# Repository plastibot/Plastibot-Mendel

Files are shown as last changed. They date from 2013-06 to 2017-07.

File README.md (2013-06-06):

Plastibot-Mendel
================

PLASTIC PARTS:

Plastic parts are released under the same license as the original author.

Refer to www.plastibot.com/credits for credits/attributions as well as license for each part.

Print the following quantities of the plastic parts. The Gcode files were sliced using settings tailored
to the Plastibot Mendel Printer. If you have a different printer you will have to slice your own files.
Use 0.25mm layer tickness and 25% infill. The Y-LM8UU holder and the X-Carriage-LM8UU-Holder requires to
add a lip of 2mm to ensure the part won't come loose half print.

1x  X-End Motor
1x  X-End Idler
1x  X-Carriage-Platform
1x  X-Carriage-Bracket
2x  X-Carriage-LM8UU-Holder
1x  Herringbone Big Gear
1x  Herringbone Small Gear
1x  Extruder (Body, idler, spacer, axle)
4x  Y-LM8UU Holder
2x  Y-Belt Clamp sets (channel, clamp and socket)
2x  endstop holder
2x  Fan Holder
2x  Spool Bushing

LASER CUT PARTS:

The Laser cut Frame is released under Creative Commons - Non Commercial Use License.

Laser cut out of 3/16" thick birch plywood. The bed plate needs to be laser cut out of 
MDF 3/8" thick.

ASSEMBLY INSTRUCTIONS

Assembly instructions can be found at:

    www.plastibot.com/assembly-instructions

Remaining parts (vitamins) to build the printer can be purchased at:

    www.plastibot.com/store

For support please contact us at support@plastibot.com

Have fun !!!

The Plastibot Team.

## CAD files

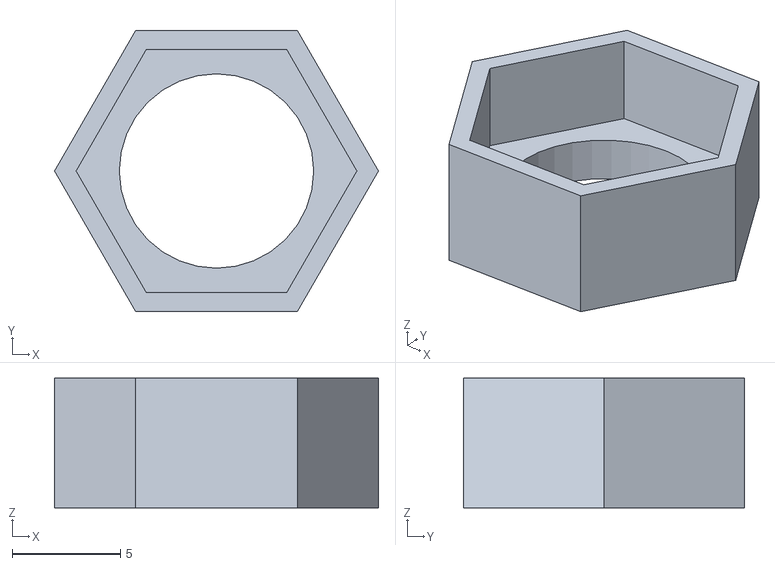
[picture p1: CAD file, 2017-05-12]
Plastic Parts/Backlash spring cup/Spring Cup Rev1.stl
15.0 x 13.0 x 6.00

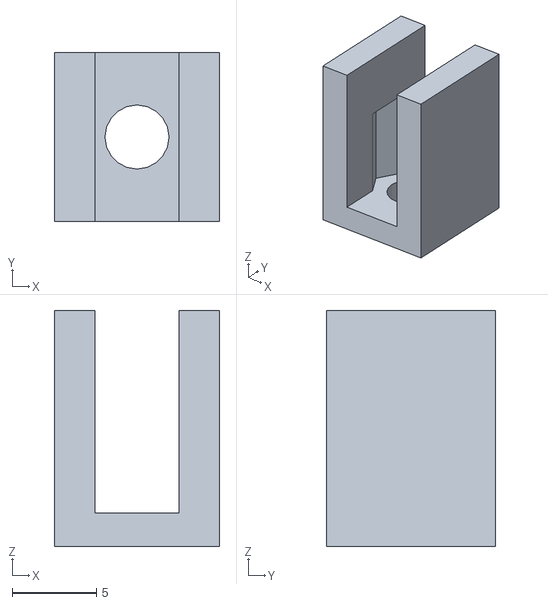
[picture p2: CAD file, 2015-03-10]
Plastic Parts/Card Bracket/Card Bracket 10.stl
9.80 x 10.0 x 14.0

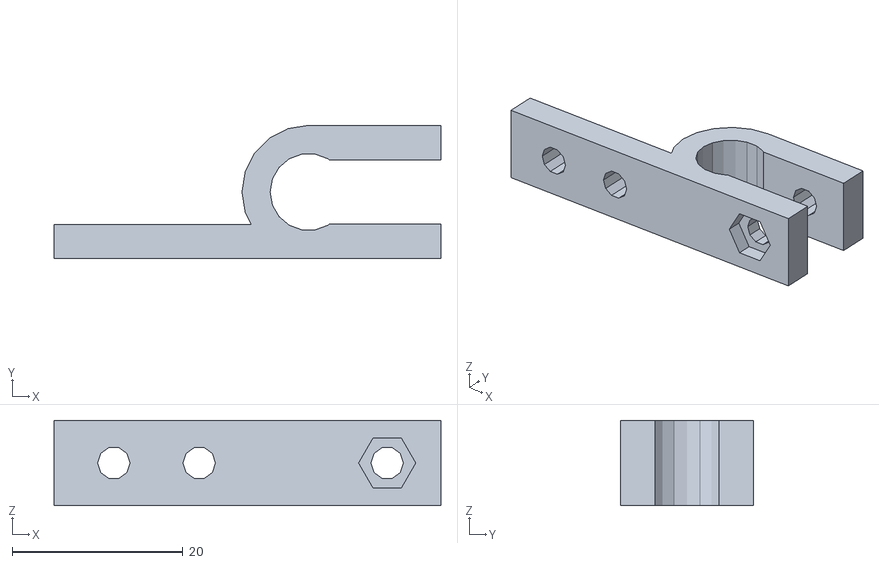
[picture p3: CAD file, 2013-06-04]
Plastic Parts/Endstop Holder/endstop_holder.stl
45.3 x 15.6 x 10.0

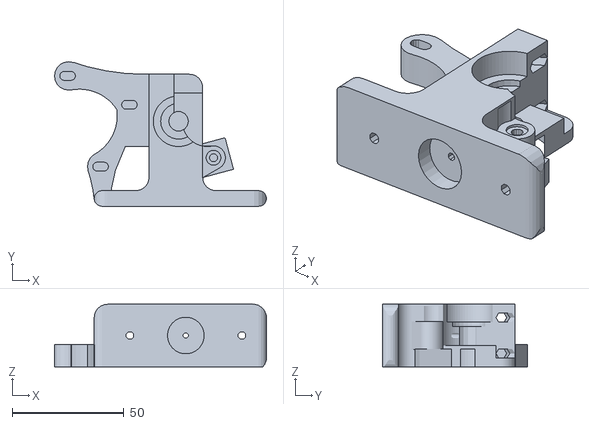
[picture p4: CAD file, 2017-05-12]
Plastic Parts/Extruder 1_75mm Primary/Extruder-primary_body-1_75-fixed.stl
94.7 x 64.6 x 28.0

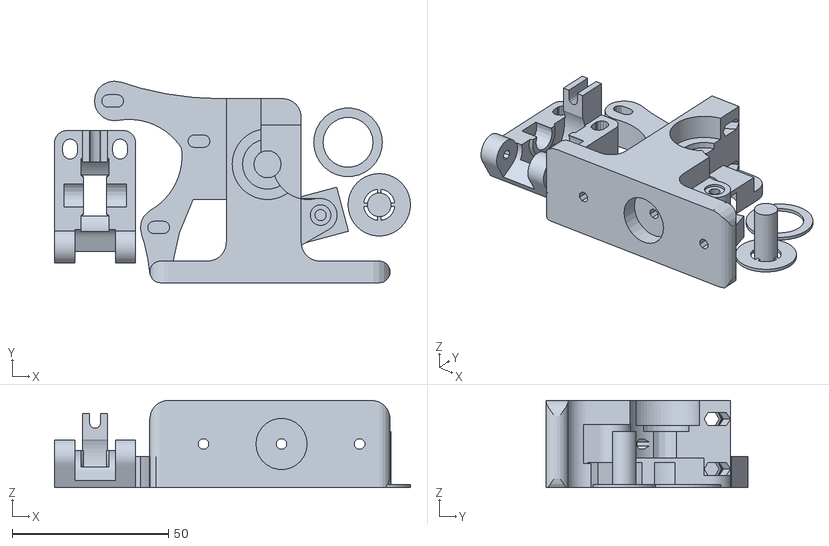
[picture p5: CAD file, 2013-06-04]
Plastic Parts/Extruder 3mm Primary/Extruder-all-parts.stl
114.0 x 64.6 x 28.0

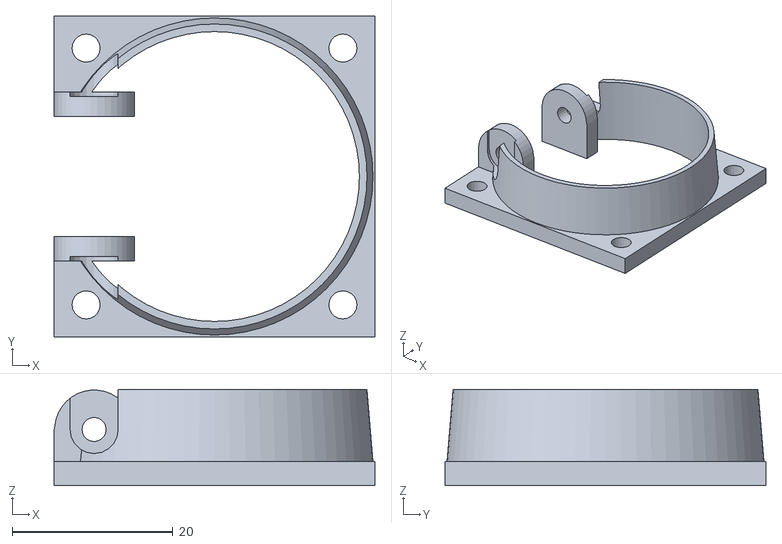
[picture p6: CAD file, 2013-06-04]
Plastic Parts/Fan holder/fanholder.stl
40.0 x 40.0 x 12.0

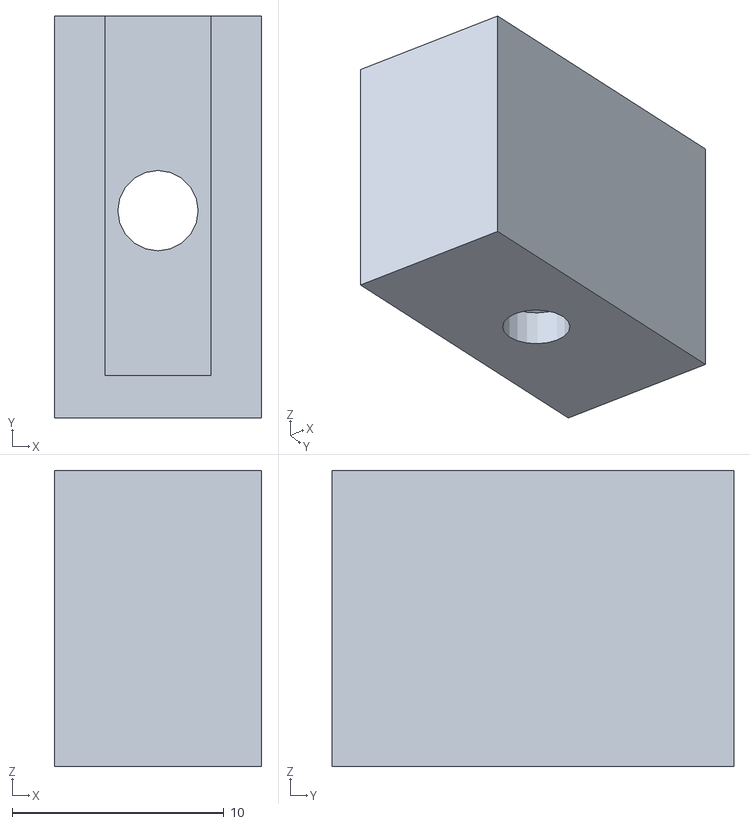
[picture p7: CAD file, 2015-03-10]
Plastic Parts/Frog Bracket/Frog Bracket Rev2.stl
9.80 x 19.0 x 14.0

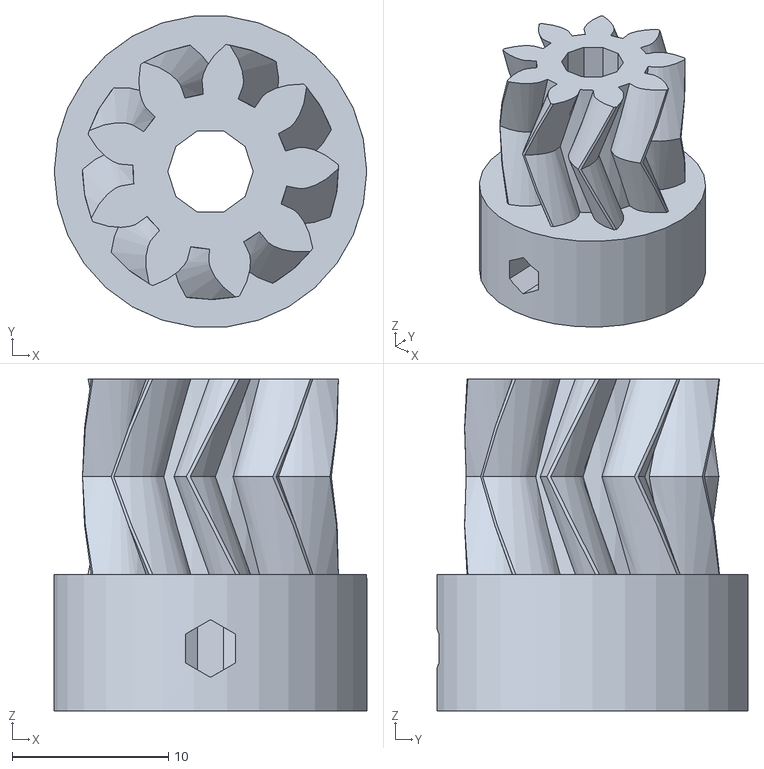
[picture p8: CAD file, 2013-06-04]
Plastic Parts/Herringbone Gears/smallgear.stl
20.0 x 19.9 x 21.2

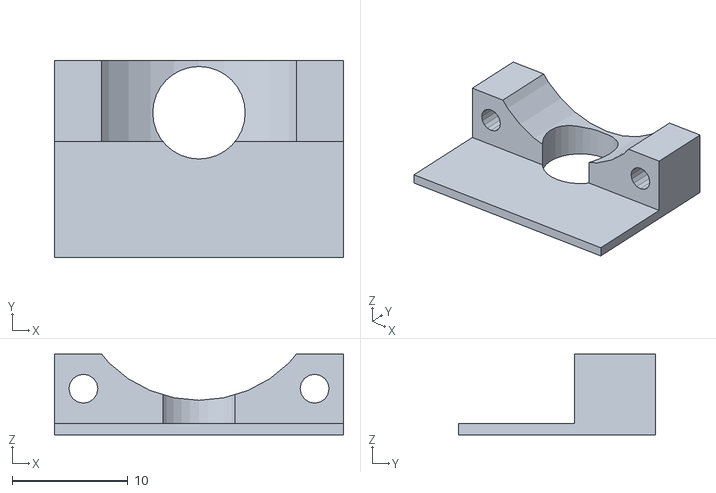
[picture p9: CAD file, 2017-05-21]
Plastic Parts/Hexagon fan/hotend_fan_rev1.stl
25.0 x 17.0 x 7.00

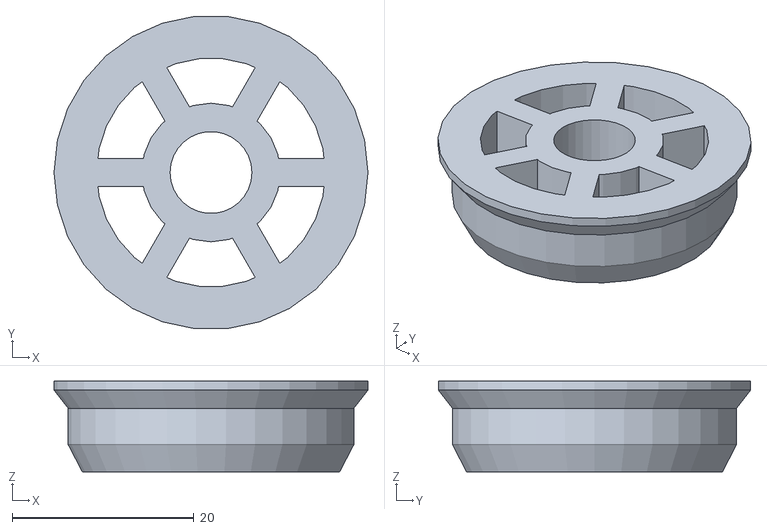
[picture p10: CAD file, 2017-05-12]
Plastic Parts/Spool Bushing/bushing-1Kg-32mm.stl
34.5 x 34.3 x 10.0

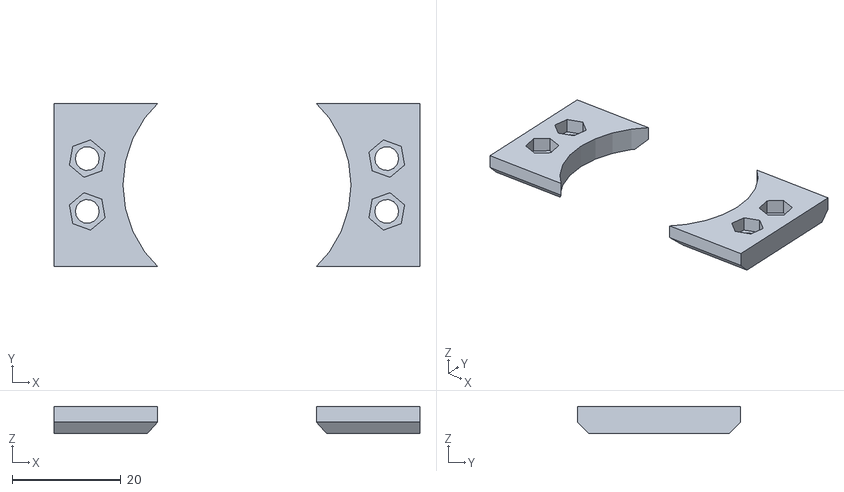
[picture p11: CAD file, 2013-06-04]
Plastic Parts/X carriage/Bracket.stl
67.4 x 30.0 x 5.00

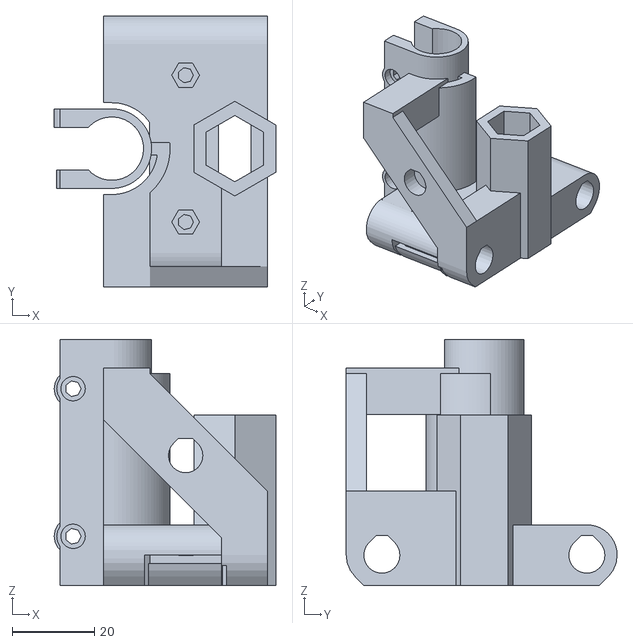
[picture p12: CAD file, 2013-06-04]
Plastic Parts/X supports/x-end-idler.stl
54.1 x 66.0 x 60.0

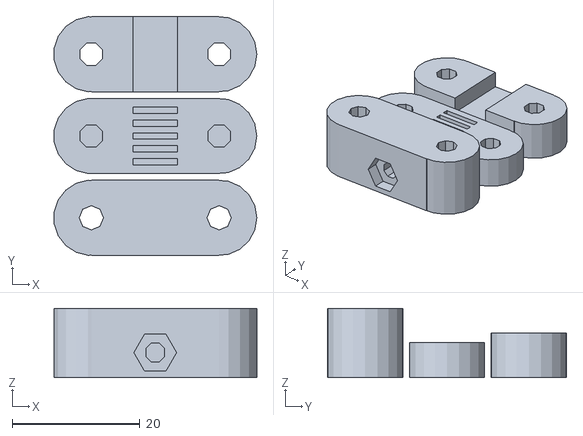
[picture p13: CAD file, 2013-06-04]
Plastic Parts/Y belt clamp/y-belt-clamp.stl
31.7 x 37.4 x 10.8

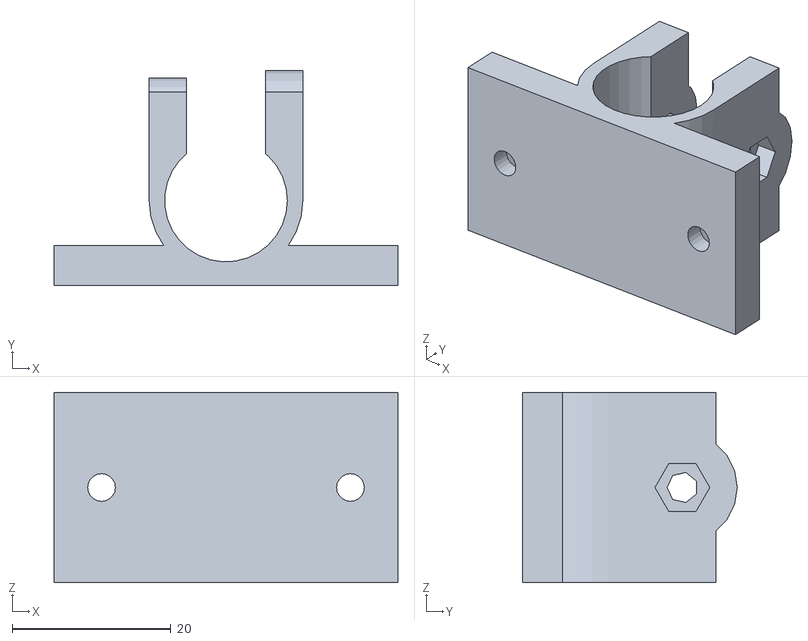
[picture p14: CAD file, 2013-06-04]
Plastic Parts/Y Carriage/y-lm8uu-holder-slim-vertical.stl
43.4 x 27.1 x 24.0

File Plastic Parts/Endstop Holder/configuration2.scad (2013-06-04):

// PRUSA Mendel  
// Configuration file
// GNU GPL v2
// Josef Průša
// josefprusa@me.com
// prusadjs.cz
// http://www.reprap.org/wiki/Prusa_Mendel
// http://github.com/prusajr/PrusaMendel

// PLEASE SELECT ONE OF THE CONFIGURATIONS BELOW
// BY UN-COMMENTING IT

variant=0; //0 for metric
//variant=1; //1 for SAE
if(variant==0){
echo("variant: metric");
}else if(variant==1){
echo("variant: sae");
} else{
echo("WARNING: INVALID CONFIGURATION");
}


vars=[
//[m8_dia, m8_nut, m4_dia, m4_nut, m3_dia, m3_nut, bush_dia, mot_shaft, bush_rod, bush_outerdia, bush_length]
[9,16,4.5,9.3,3.8,6.7,11,5.3,8,16,11],//metric M8 was 15.8
[9,15.4,4.5,9.3,4.5,9.3,11.5,5.3,7.9375,16,11]//SAE
];

//BUSHING TYPE Can generate three versions
// 1 - regular old ones
// 2 - helical ones
// 3 - holders for brass or any other bought bushings
bushing_type = 2;

//Round corner diameter
round_corner_diameter = 8;

//Thin wall size
layer_height = 0.4;
perimeter_width_over_thicknes = 1.6;
infill_widht_over_thickness = 1.55;
thin_wall = 2*(perimeter_width_over_thicknes*layer_height+infill_widht_over_thickness*layer_height);
if(thin_wall<2){
	echo("Check thin wall size, its below 2mm!");
}
echo(thin_wall);

//DO NOT TOUCH THIS SECTION!
m8_diameter = vars[variant][0];
m8_nut_diameter = vars[variant][1];
m4_diameter = vars[variant][2];
m4_nut_diameter = vars[variant][3];
m3_diameter = vars[variant][4];
m3_nut_diameter = vars[variant][5];
bushing_diameter = vars[variant][6];
motor_shaft=vars[variant][7];
bushing_rodsize = vars[variant][8];
bushing_outerDiameter = vars[variant][9];
bushing_lenght = vars[variant][10];


// MINI-HUXLEY VERSION (TODO, just place holder)
// include <configuration-huxley.scad>

// MEGA VERSION (TODO, just place holder)
// include <configuration-mega.scad>


// Some basic functions, probably should be somewhere else
module roundcorner(diameter){
	difference(){
		cube(size = [diameter,diameter,99], center = false);
		translate(v = [diameter, diameter, 0]) cylinder(h = 100, r=diameter, center=true);
	}
}

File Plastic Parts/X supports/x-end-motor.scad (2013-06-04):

// PLASTIBOT MENDEL
// X-end-motor.
// Added room for 32T pulley. Added screw for Z endstop fine adjustment.
// Plastibot <support@plastibot.com>
// Derived from: 

// Improved X ends for Prusa with clamped rods
// by Jonas Kuehling
// http://www.thingiverse.com/thing:18384



use <jonaskuehling-default.scad>
include <lm8uu-holder-slim_double-vertical.scad>



$fa =0.01;
$fs = 1;

// PARAMETERS
rod_dia = 8.4; // was 8
rod_dist = 50;		// center to center
zrod_leadscrew_dist = 30;
clearance = 0.2;		// default clearance
wall = 3;			// default wall thickness
wall_thin = 3;
xend_body_length = 40;

m3_screw_dia = 3; //was 3
m3_screw_head_dia = 6;
m3_screw_head_height = 3;
m3_nut_wrench_size = 5.5; //was 5.5
m3_nut_height = 2.4;

m8_screw_dia = 8; //was 8
m8_washer_dia = 16;
m8_washer_height = 1.5;

idler_dia = 22;		// when using pure 608 bearing without belt guide: 22mm - was 25

belt_rod_dist = 7.5;		// in y direction
belt_elevation = 6.5;		// in z direction, space between rod top and belt bottom;
						// = distance between upper side of rods and upper platform of x-carriage (with belt clamps)
belt_height = 2.6;		// belt thickness..

xmotor_y_offset = 45;
idler_y_offset = rod_dist/2+rod_dia/2+belt_rod_dist - 2*m8_washer_height;

// belt range = rod_dist/2+rod_dia/2+belt_rod_dist - nema17 shaft socket = 36.5 - 43 = 6.5mm

leadscrew_dia = 7; // was 8
leadscrew_nut_wrench_size = 13.4+0.2;		// plus some extra clearance - was 13
leadscrew_nut_height = 6.8;
anti_backlash_spring_space = 25;

nema17_width = 43;
nema17_hole_dist = 31;
nema17_center_dia = 25;

layer_height = 0.25; // was 0.25

xend_body_x_offset = 3;
motor_mount_x_offset = -2;


// CALCULATIONS
xend_body_height = rod_dia+2*clearance+2*wall;
xend_body_width = rod_dist+rod_dia+2*wall;
leadscrew_nuttrap_height = 2*leadscrew_nut_height+wall+anti_backlash_spring_space;
bearing_support_height = leadscrew_nuttrap_height;
idler_elevation = xend_body_height/2+rod_dia/2+belt_elevation+belt_height+idler_dia/2;


// RENDER
// "idler=false" for motor-x-end, "idler=true" for idler-x-end

assembly(idler=false);


difference() {
	union() {
		assembly(idler=false);
		//translate([-17.5, 45, 31.75]) rotate([90, 0, 0]) difference() {
			//cylinder(r=27, h=10);
			//cylinder(r=16, h=50, center=true);
			//rotate([0, 0, 6]) translate([-17, 0, -50]) cube([100, 100, 100]);
			//rotate([0, 0, -30]) translate([-9, -50, -50]) cube([100, 100, 100]);
		//}
		translate([-38,18,0]) difference() {
			cube([10,15,10]);
			translate([5,5,0])
				polyhole(m3_screw_dia+2*clearance,xend_body_height+10);
			translate([5,5,0])
				nut_trap(m3_nut_wrench_size,m3_nut_height+1.6);
		}
		translate([-38,17,m3_nut_height-0.4])
			cube([10,15,0.4]);	
	}
	translate([-17.5, 50, 31.75]) rotate([90, 0, 0]) {
		cylinder(r=15, h=20);
		translate([0, -13, 0]) cube([100, 26, 20]);
		


	}
}




// -------------------------------------------------

module rod_mount(){
	difference(){
		// block for rods
		translate([0,(rod_dist/2+rod_dia/2+wall)/2,0])
			cube([xend_body_length,rod_dist/2+xend_body_height/2,xend_body_height],center=true);
	
		// round corners horizontal
		translate([xend_body_length/2,rod_dist/2+xend_body_height/2,xend_body_height/2])
			rotate([180,90,0])
				roundcorner(xend_body_height/2,xend_body_length);
		translate([xend_body_length/2,rod_dist/2+xend_body_height/2,-xend_body_height/2])
			rotate([0,0,180]) 
				roundcorner_tear(xend_body_height/2,xend_body_length);
	
		// rod hole
		translate([0,rod_dist/2,0]) teardropcentering(rod_dia/2+clearance,xend_body_length+2);
	
		// rod clamp
		translate([0,body_width/2+1,0])
		difference(){
			translate([0,(rod_dist/2+rod_dia/2+wall+1)/2,-(rod_dia/2+wall+1)/2])
				cube([xend_body_length-20,rod_dist/2+rod_dia/2+wall+1,rod_dia/2+wall+1],center=true);
			translate([0,(rod_dist/2+rod_dia/2+wall+1)/2,-(rod_dia/2+wall+1)/2-2])
				cube([xend_body_length-20-2,rod_dist/2+rod_dia/2+wall+1+2,rod_dia/2+wall+1],center=true);
		}
		translate([0,rod_dist/2,-0.1]) teardropcentering_half(rod_dia/2+clearance+1,xend_body_length-20-2-4,bottom=1);
		

		// clamp screw + nut trap + screw-head-trap
		translate([0,rod_dist/2-rod_dia/2-m3_screw_dia/2-2*clearance-1,0])
			polyhole(m3_screw_dia+2*clearance,xend_body_height+2);
		translate([0,rod_dist/2-rod_dia/2-m3_screw_dia/2-2*clearance-1,xend_body_height/2-m3_nut_height/2+0.5])
			nut_trap(m3_nut_wrench_size,m3_nut_height+1);
	}

	// screw hole print support
	translate([0,rod_dist/2-rod_dia/2-m3_screw_dia/2-2*clearance-1,layer_height/2+(xend_body_height/2-layer_height*round((xend_body_height/2)/layer_height))])
		polyhole(m3_screw_dia+2*clearance,layer_height);
}



module bearing_holder(){
	// linear bearing holder
	translate([-zrod_leadscrew_dist/2,0,0])
		rotate([0,0,90])
			lm8uu_holder_slim_double_vertical();
}

module bearing_holder_spacer(){
	render()
	translate([-body_width/2-zrod_leadscrew_dist/2,0,body_length/2])
		cube([body_width,body_width+3,body_length+2], center = true);
	difference(){
		translate([-zrod_leadscrew_dist/2,0,-1])
			cylinder(r=body_width/2+1.5, h=body_length+2);
		translate([body_width/2-zrod_leadscrew_dist/2+body_width/2-0.5,0,body_length/2])
			cube([body_width,body_width+3,body_length+2], center = true);
	}
}



module leadscrew_nuttrap(){
	translate([zrod_leadscrew_dist/2,0,0])
		rotate([0,0,30]){
			translate([0,0,leadscrew_nuttrap_height/2])
				difference(){
					nut_trap(leadscrew_nut_wrench_size+2*wall,leadscrew_nuttrap_height);
					nut_trap(leadscrew_nut_wrench_size,leadscrew_nuttrap_height+2);
				}
			translate([0,0,wall/2+leadscrew_nut_height])
				difference(){
					nut_trap(leadscrew_nut_wrench_size+2*wall,wall);
					rotate([0,0,-30]) cube([leadscrew_dia+1,leadscrew_nut_wrench_size*2,wall+2],center=true);
				}
		}
}

module leadscrew_nuttrap_spacer(){
	translate([zrod_leadscrew_dist/2,0,leadscrew_nuttrap_height/2])
	rotate([0,0,30])
		nut_trap(leadscrew_nut_wrench_size+2*wall,leadscrew_nuttrap_height+2);
}



nema17_hole1 = [nema17_hole_dist/2,nema17_hole_dist/2];
nema17_hole2 = [nema17_hole_dist/2,-nema17_hole_dist/2];
nema17_hole3 = [-nema17_hole_dist/2,nema17_hole_dist/2];
nema17_hole4 = [-nema17_hole_dist/2,-nema17_hole_dist/2];

module motor_mount(){
	difference(){
		union(){
			translate([-nema17_hole_dist/2+motor_mount_x_offset,xmotor_y_offset,
						nema17_hole_dist/2+xend_body_height+m3_screw_dia/2+clearance])
				difference(){
					union(){
						rotate([90,0,0])
							linear_extrude(height=10){
								barbell(nema17_hole3,nema17_hole4,
										(nema17_width-nema17_hole_dist)/2,(nema17_width-nema17_hole_dist)/2,
										20,60);
								barbell(nema17_hole4,nema17_hole2,
										(nema17_width-nema17_hole_dist)/2,(nema17_width-nema17_hole_dist)/2,
										20,60);
							}
		
						// nema17 mount bottom support
						translate([0,-10-(xmotor_y_offset-10-rod_dist/2)/2,
									-xend_body_height/2-nema17_hole_dist/2-m3_screw_dia/2-clearance])
							cube([nema17_width,xmotor_y_offset-10-rod_dist/2,xend_body_height],center=true);
						translate([0,-5,-(xend_body_height+m3_screw_dia/2+clearance)/2-nema17_hole_dist/2])
							difference(){
								cube([nema17_width,10,(xend_body_height+m3_screw_dia/2+clearance)],center=true);

								// round corner bottom x direction
								translate([nema17_width/2,5,-(xend_body_height+m3_screw_dia/2+clearance)/2])
									rotate([0,0,180]) 
										roundcorner_tear(xend_body_height/2,nema17_width);
							}
					}
		
					// nema17 screw holes
					for(k=[1,-1]) for(l=[1,-1])
						translate([k*nema17_hole_dist/2,-5,l*nema17_hole_dist/2])
							rotate([0,0,90]) teardrop(m3_screw_dia/2+clearance,12);
		
					// xend body cut off 1
					translate([0,-(xmotor_y_offset-rod_dist/2)-0.1,-(xend_body_height/2+m3_screw_dia/2+clearance)-nema17_hole_dist/2])
						rotate([180,0,0])
							teardropcentering(xend_body_height/2,nema17_width+2);

					// round corner bottom y direction
					translate([-nema17_width/2,5,-nema17_hole_dist/2-m3_screw_dia/2-clearance-xend_body_height])
						rotate([0,0,-90]) 
							roundcorner_tear(xend_body_height/2,nema17_width);
				}
		
			// nema17 mount top support
			translate([0,0,nema17_hole_dist+(m3_screw_head_dia+2*clearance)/2+xend_body_height+m3_screw_dia/2+clearance])
				linear_extrude(height=5)
					polygon(points=[[-xend_body_length/2+xend_body_x_offset,body_width/2+1.5],[-xend_body_length/2+xend_body_x_offset+10,body_width/2+1.5],
										[-nema17_hole_dist+motor_mount_x_offset+5,xmotor_y_offset],
										[-nema17_hole_dist+motor_mount_x_offset-5,xmotor_y_offset]]);

			translate([-nema17_hole_dist+motor_mount_x_offset,-5+xmotor_y_offset,nema17_hole_dist+xend_body_height+m3_screw_dia/2+clearance+(5+m3_screw_head_dia/2+clearance)/2])
				cube([10,10,5+m3_screw_head_dia/2+clearance],center=true);
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

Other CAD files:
Lasercut Parts/Plastibot Mendel Rev2.6.dwg
Plastic Parts/Backlash spring cup/Spring Cup.stl
Plastic Parts/Card Bracket/Card Bracket 15.stl
Plastic Parts/Extruder 1_75mm Primary/Extruder-idler-primary-1_75.stl
Plastic Parts/Herringbone Gears/parametric_involute_gear_v5.0.scad
Plastic Parts/Backlash spring cup/Spring Cup Rev1.scad
Plastic Parts/Backlash spring cup/Spring Cup.scad
Plastic Parts/Bed-Corners/Bed-Corner-std-nut-3_5mm.scad
Plastic Parts/Bed-Corners/Bed-Corner-std-nut-3_5mm.stl
Plastic Parts/Card Bracket/Card Bracket.scad
Plastic Parts/Endstop Holder/endstop-holder.scad
Plastic Parts/Extruder 1_75mm Primary/Extruder-all-parts-1_75.scad
Plastic Parts/Extruder 3mm Primary/Extruder-all-parts.scad
Plastic Parts/Extruder 3mm Primary/configuration.scad
Plastic Parts/Extruder 3mm Primary/functions.scad
Plastic Parts/Extruder 3mm Primary/gregs-wadebits.scad
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

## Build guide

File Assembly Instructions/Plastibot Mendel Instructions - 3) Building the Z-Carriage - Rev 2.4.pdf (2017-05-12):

# Mendel 3D Printer Assembly

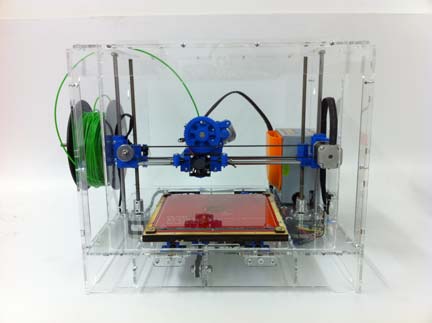
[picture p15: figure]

# Section 3

# Z-Carriage Assembly

## Step 1: Adding the backlash mechanism

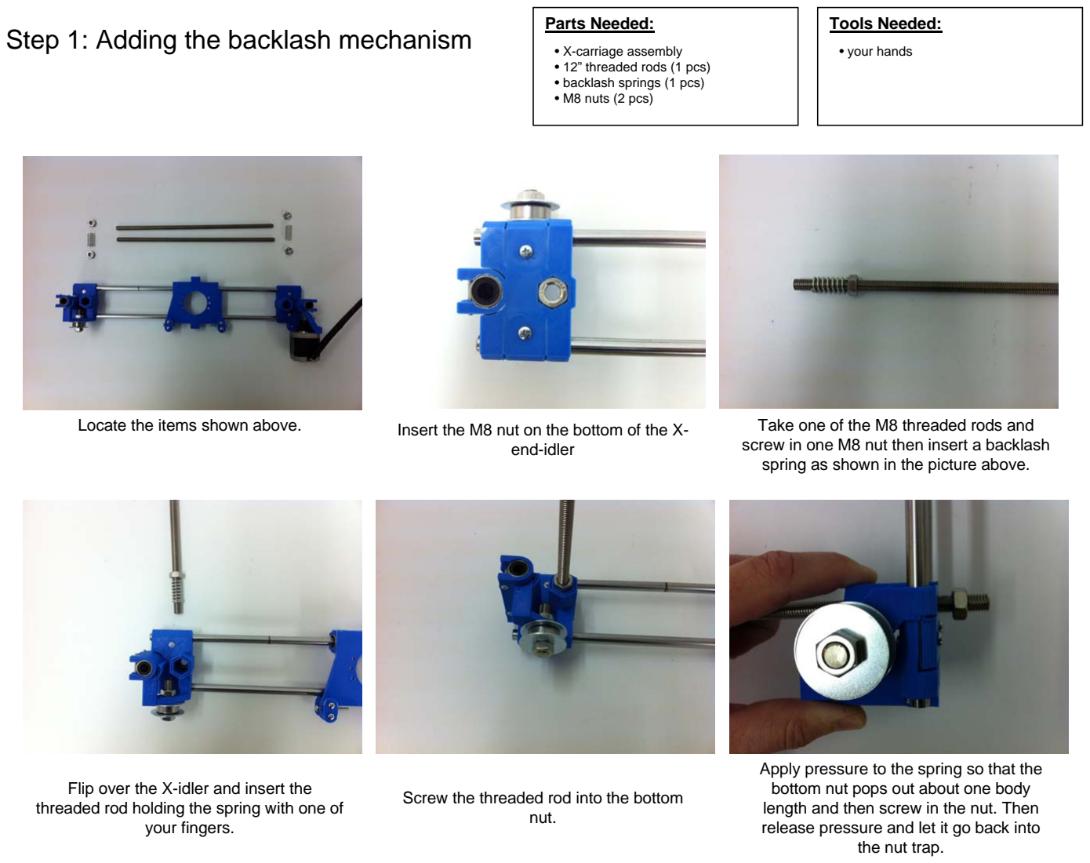
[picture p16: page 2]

Parts Needed:

- X-carriage assembly
- 12” threaded rods (1 pcs)
- backlash springs (1 pcs)
- M8 nuts (2 pcs)

Tools Needed:

- your hands
Locate the items shown above. | Take one of the M8 threaded rods and screw in one M8 nut then insert a backlash spring as shown in the picture above.

Flip over the X-idler and insert the threaded rod holding the spring with one of your fingers.

Apply pressure to the spring so that the bottom nut pops out about one body length and then screw in the nut. Then release pressure and let it go back into the nut trap.

Insert the M8 nut on the bottom of the X-end-idler

Screw the threaded rod into the bottom nut.

## Step 2: Adding the backlash mechanism

(Cont).

Parts Needed:

- X-carriage assembly
- 12” threaded rods (1 pcs)
- backlash springs (1 pcs)
- M8 nuts (2 pcs)

Tools Needed:

- Your hands

Repeat the same steps done on previous page this time for X-end-Motor. Take the second threaded rod, screw-in a nut and insert the backlash spring.

Screw in the bottom nut.

Apply pressure to the spring so that the bottom nut pops out about one body length and then screw in the nut.

This is how it should look now.

Insert the threaded rod with the nut and backlash spring from the top of the X-end-motor assembly

Then release pressure and let it go back into the nut trap.

## Step 3: Adding couplings

Parts Needed:

- X-carriage assembly
- Couplings ( 2 pcs)

Tools Needed:

- Allen Key #2 (Metric)
Locate the parts shown above. | Use the #2 Allen key to unscrew the setscrew until it doesn’t show anymore..

This I show the hole should look after unscrewing the setscrew. Make sure you do this on both holes of each coupling.

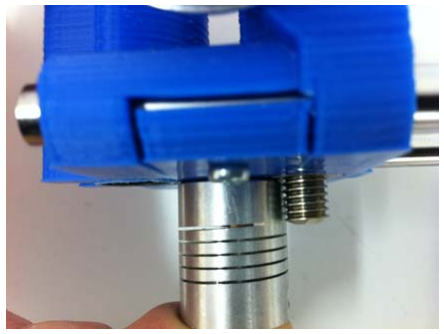
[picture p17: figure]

Face the coupling against the bottom surface right next to the threaded rod and screw in or out the threaded rod so that the end of the threaded rod is where the spiral on the coupling starts.

Make sure the setscrews on the couplings are not obstructing the hole. In this case you can see the setscrew protruding.

Find the hole on the coupling with the bigger diameter

## Step 4: Adding couplings (cont.)

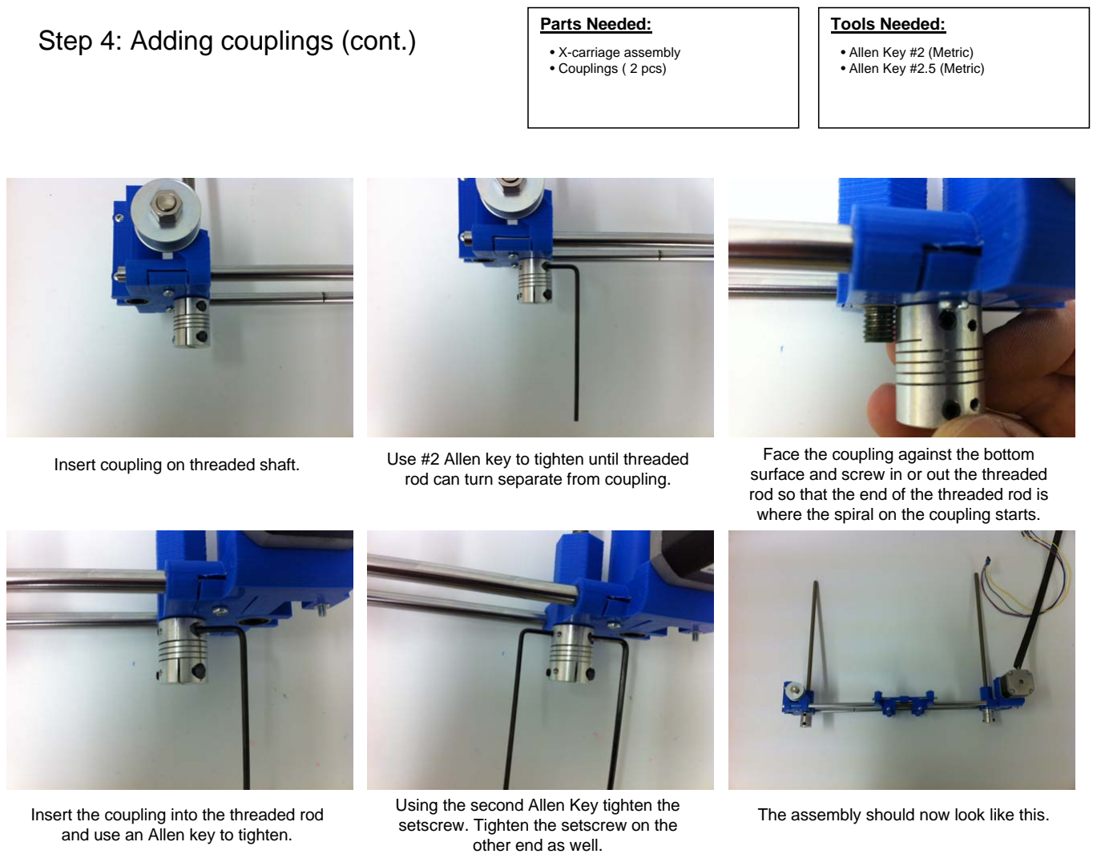
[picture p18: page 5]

Parts Needed:

- X-carriage assembly
- Couplings ( 2 pcs)

Tools Needed:

- Allen Key #2 (Metric)
- Allen Key #2.5 (Metric)
Insert coupling on threaded shaft. | Face the coupling against the bottom surface and screw in or out the threaded
| rod so that the end of the threaded rod is where the spiral on the coupling starts.

Insert the coupling into the threaded rod and use an Allen key to tighten.

The assembly should now look like this.

Use #2 Allen key to tighten until threaded rod can turn separate from coupling.

Using the second Allen Key tighten the setscrew. Tighten the setscrew on the other end as well.

Step 5: Adding Left side Z Smooth rod Parts Needed: • X-carriage assembly • Frame Assembly • Z smooth rods (2 pcs)

Tools Needed:

- Your hands

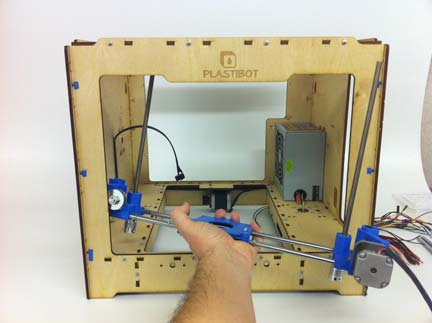
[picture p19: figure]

Take the assembly previously finished and carefully insert it into the frame using the Front window (window with the plastibot logo)

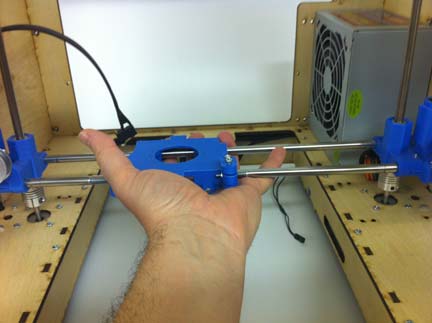
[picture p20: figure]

Align the couplings to the Z-motor shafts and let them sit on top of the shafts

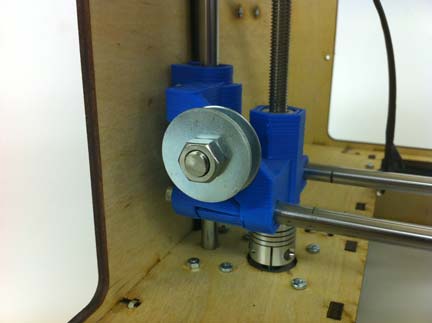
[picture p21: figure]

Align the smooth rod with the bottom hole and push the smooth rod all the way into the bottom panel.

Continue to push down the smooth rod from the top until the rod is flush (or a couple mm) on the top panel

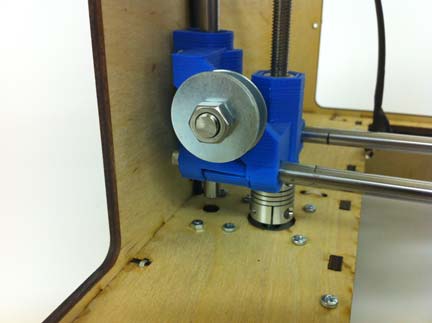
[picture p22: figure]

Align the left side linear bearings with the smooth rod. Keep them as parallel as possible and insert the rod thru the linear bearings.

Insert the Left side Z smooth rod into the hole on the Top Assembly and Lower it to just before the X-end-idle Linear bearings.

NOTE: If the smooth rods are not completely parallel when inserted into the linear bearings, some of the balls on the linear bearing will pop out. That is normal as long as you only get a couple or so out.

Step 6: Adding right side Z Smooth rod Parts Needed: • X-carriage assembly • Frame Assembly • Z smooth rods (2 pcs) • Zip Ties (2 pcs)

Tools Needed:

- Your hands

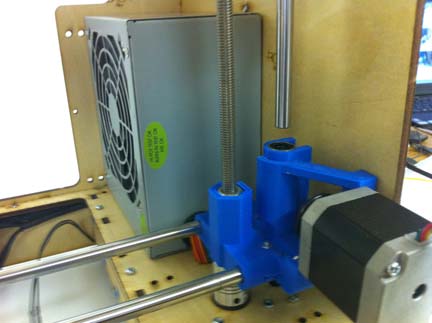
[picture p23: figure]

Insert the Right side Z smooth rod into the hole on the Top Assembly and Lower it to just before the X-end-motor Linear bearings

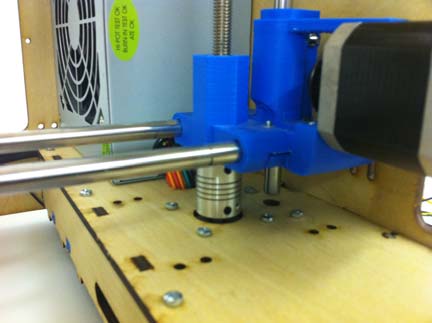
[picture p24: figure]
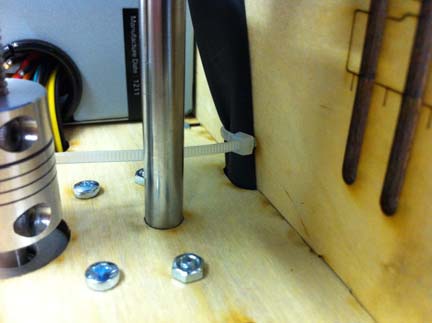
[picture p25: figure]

Use a zip tie to secure the wire harness in place to the left panel at the bottom section.

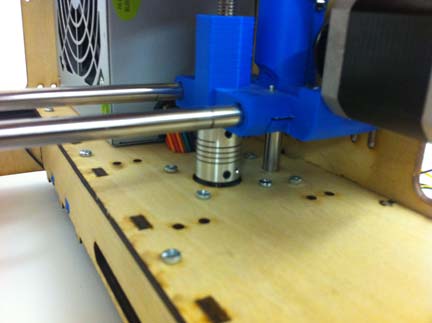
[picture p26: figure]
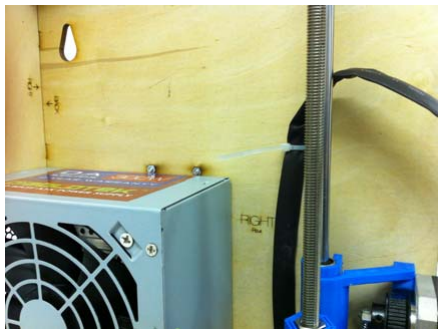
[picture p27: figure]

Use a second zip tie to secure to the left panel at the middle section.

Continue to push down the smooth rod from the top until the rod is flush (or a couple mm) on the top panel.

Align the smooth rod with the bottom hole and push the smooth rod all the way into the bottom panel.

NOTE: If the smooth rods are not completely parallel when inserted into the linear bearings, some of the balls on the linear bearing will pop out. That is normal as long as you only get a couple or so out.

Align the Right side linear bearings with the smooth rod. Keep them as parallel as possible and insert the rod thru the linear bearings.

## Step 7: Tightening couplings to motor shaft

Parts Needed:

- Frame assembly
- laser cut caps (2 pcs)

Tools Needed:

- Allen Key #2 (Metric)
- Allen Key #2.5 (Metric)

Use #2.5 Allen key to tighten the coupler to the motor shaft. If there isn’t enough room to turn the Allen key, then turn the 2 threaded rods to raise the Z axis

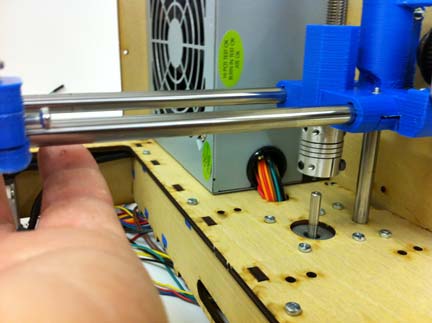
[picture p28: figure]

Align the couplings on both ends to the motor shafts and insert if they arent inserted already.

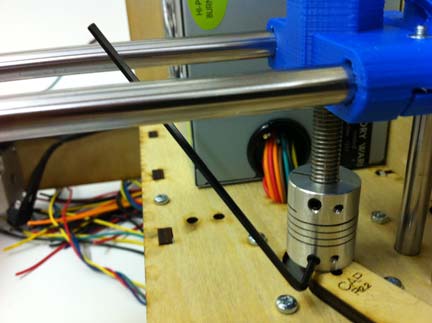
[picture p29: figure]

Use Allen key #2 to tighten the setscrew, then remove the laser cut cap

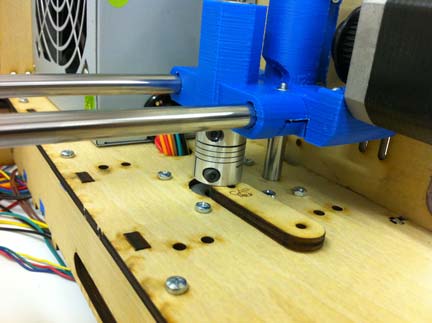
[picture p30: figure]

Put one of the laser cut plywood cap under the coupling as a spacer gage as shown here. Do the same on the other coupling.

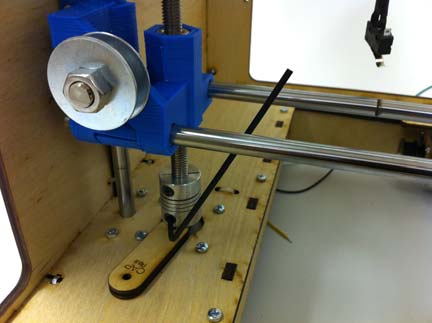
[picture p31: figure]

Repeat for the other side. Use #2.5 Allen key to tighten the coupler to the motor shaft

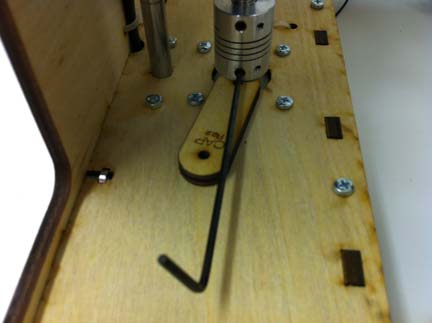
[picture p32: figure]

Use Allen key #2 to tighten the setscrew, then remove the laser cut cap.

## Step 8: Installing the belt

Parts Needed:

- Frame Assembly
- Timing belt

Tools Needed:

- philips screwdriver

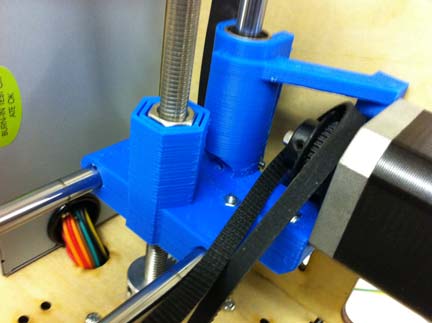
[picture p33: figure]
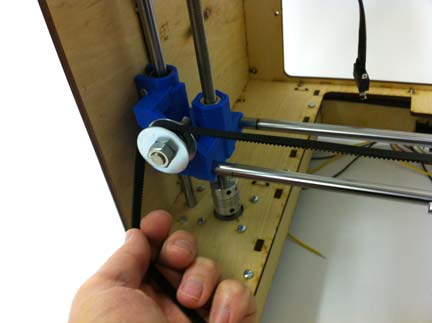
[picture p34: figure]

Take the opposite end of the belt and wrap it around the idler.

Put your finger on top of the belt on the upper side of the pulley. Use your other hand to pull away the X-Carriage so that the pulley rotates while guiding the belt with your finger.

Locate one of the timing belts and unroll it.

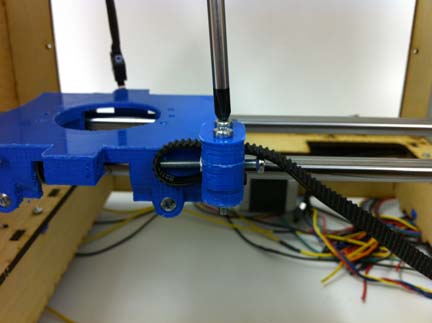
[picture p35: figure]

Start by clamping one end of the belt on the right side clamp. The belt teeth should be facing up. Use a screwdriver to tighten.

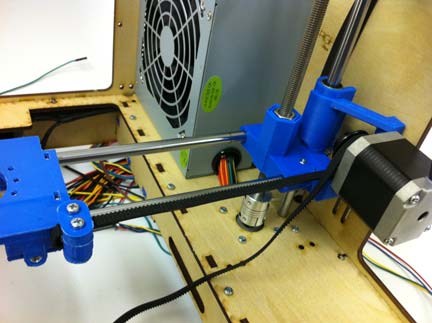
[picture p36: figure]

The belt will align into position on the bottom.

Take the belt and wrap it around the pulley from bottom to top. Most likely you won’t be able to get the belt inserted on the bottom as there is little gap. That is fine.

## Step 9: Installing the belt (cont.)

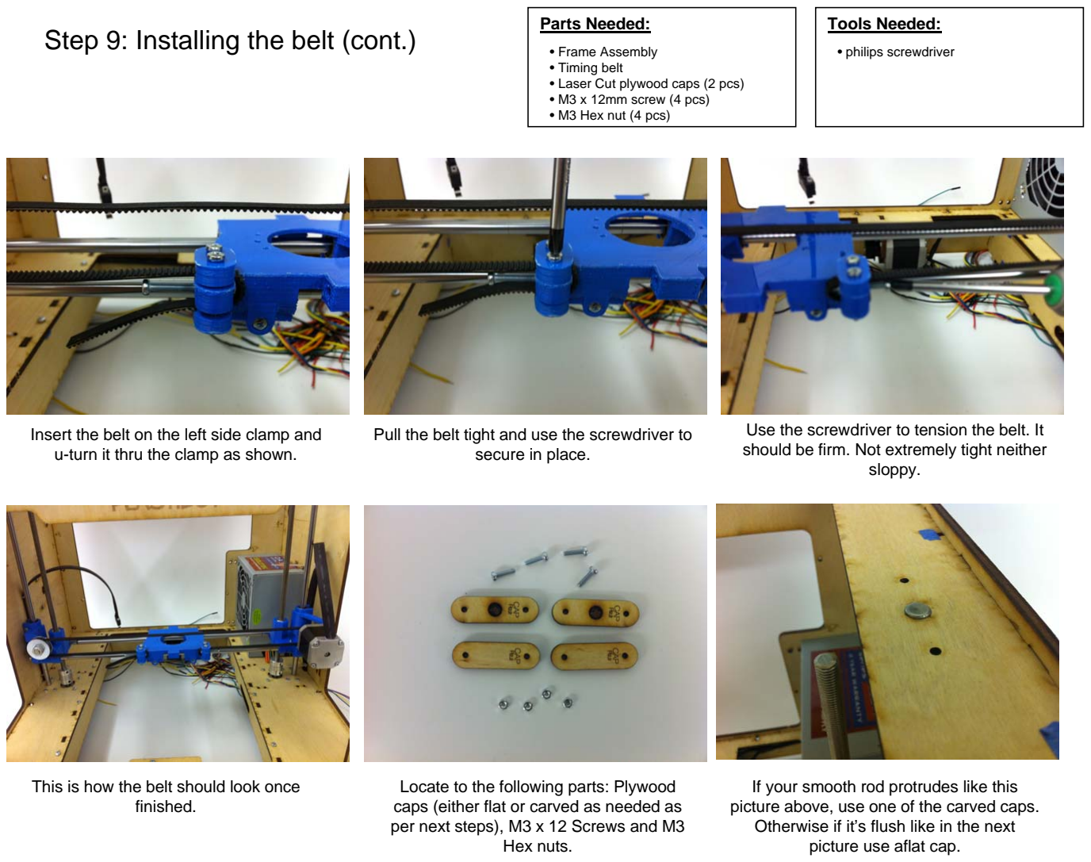
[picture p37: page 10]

Parts Needed:

- Frame Assembly
- Timing belt
- Laser Cut plywood caps (2 pcs)
- M3 x 12mm screw (4 pcs)
- M3 Hex nut (4 pcs)

Tools Needed:

- philips screwdriver

Use the screwdriver to tension the belt. It should be firm. Not extremely tight neither sloppy.

This is how the belt should look once finished.

Insert the belt on the left side clamp and u-turn it thru the clamp as shown.

Locate to the following parts: Plywood caps (either flat or carved as needed as per next steps), M3 x 12 Screws and M3 Hex nuts.

Pull the belt tight and use the screwdriver to secure in place.

If your smooth rod protrudes like this picture above, use one of the carved caps. Otherwise if it’s flush like in the next picture use aflat cap.

## Step 10 Adding Rod caps

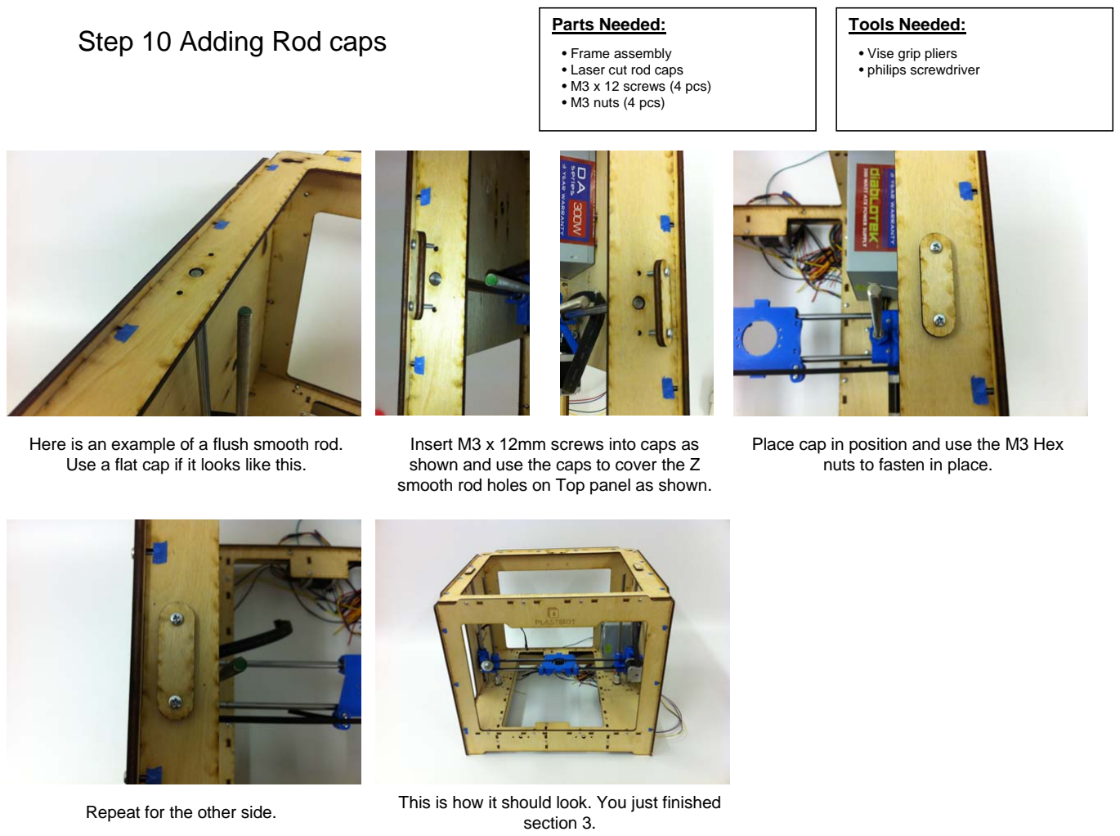
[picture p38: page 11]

Parts Needed:

- Frame assembly
- Laser cut rod caps
- M3 x 12 screws (4 pcs)
- M3 nuts (4 pcs)

Tools Needed:

- Vise grip pliers
- philips screwdriver

This is how it should look. You just finished section 3.

Here is an example of a flush smooth rod. Use a flat cap if it looks like this.

Place cap in position and use the M3 Hex nuts to fasten in place.

Insert M3 x 12mm screws into caps as shown and use the caps to cover the Z smooth rod holes on Top panel as shown.

Repeat for the other side.

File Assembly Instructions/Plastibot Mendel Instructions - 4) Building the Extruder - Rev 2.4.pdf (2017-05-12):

# Mendel 3D Printer Assembly


# Section 4

# Extruder Assembly

## Step 1: Cleaning plastic parts

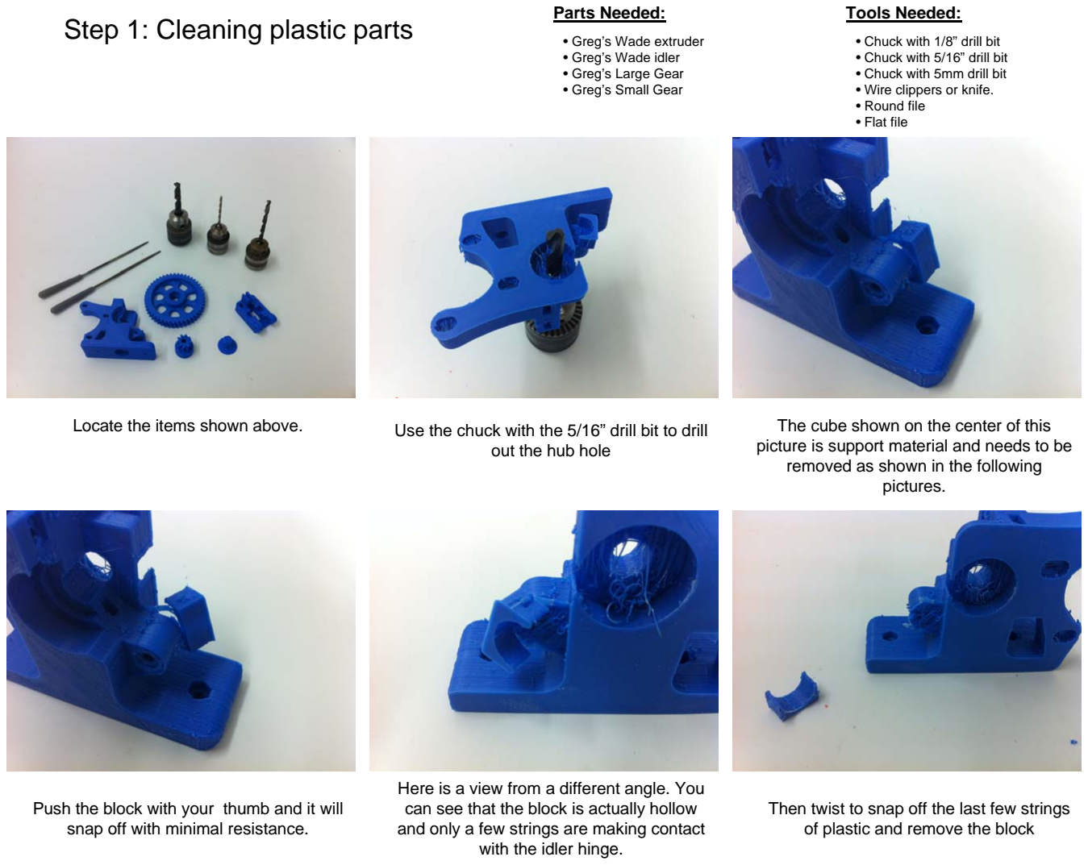
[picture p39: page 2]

Parts Needed:

- Greg’s Wade extruder
- Greg’s Wade idler
- Greg’s Large Gear
- Greg’s Small Gear

Tools Needed:

- Chuck with 1/8” drill bit
- Chuck with 5/16” drill bit
- Chuck with 5mm drill bit
- Wire clippers or knife.
- Round file
- Flat file
Locate the items shown above. | The cube shown on the center of this picture is support material and needs to be removed as shown in the following pictures.

Push the block with your thumb and it will snap off with minimal resistance.

Then twist to snap off the last few strings of plastic and remove the block

Use the chuck with the 5/16” drill bit to drill out the hub hole

Here is a view from a different angle. You can see that the block is actually hollow and only a few strings are making contact with the idler hinge.

Step 2: Cleaning plastic parts (Cont).

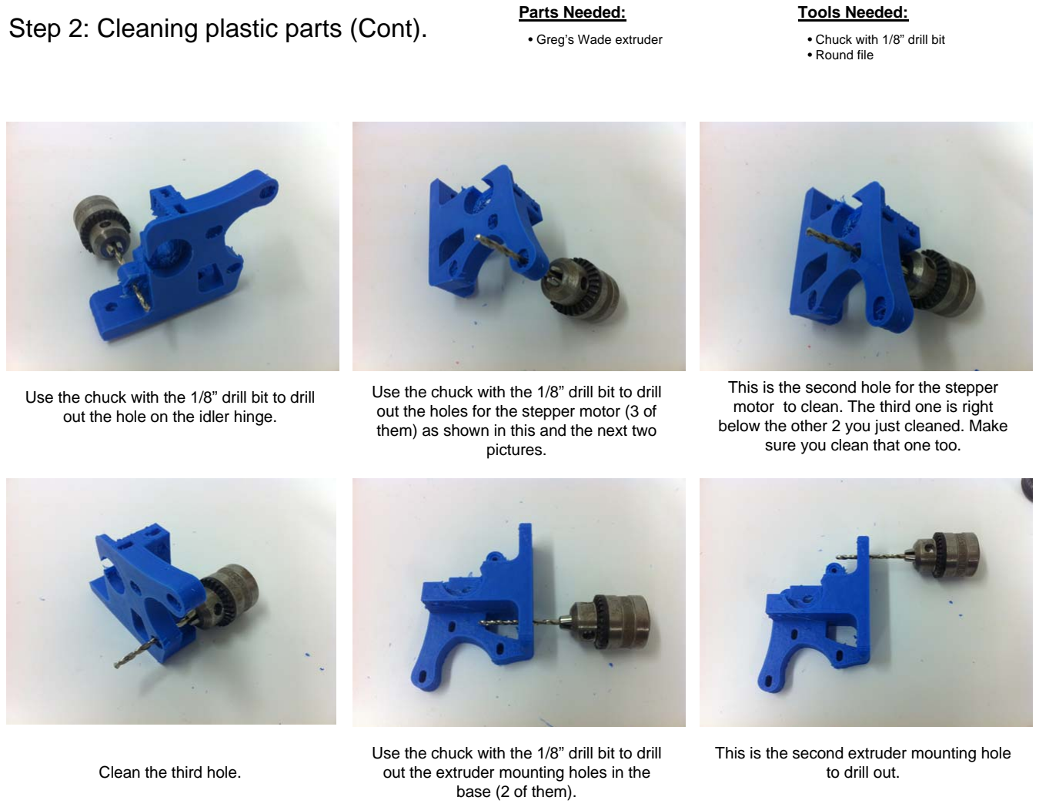
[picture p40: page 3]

Parts Needed:

- Greg’s Wade extruder

Tools Needed:

- Chuck with 1/8” drill bit
- Round file

Use the chuck with the 1/8” drill bit to drill out the hole on the idler hinge.

This is the second hole for the stepper motor to clean. The third one is right below the other 2 you just cleaned. Make sure you clean that one too.

Use the chuck with the 1/8” drill bit to drill out the extruder mounting holes in the base (2 of them).

Use the chuck with the 1/8” drill bit to drill out the holes for the stepper motor (3 of them) as shown in this and the next two pictures.

This is the second extruder mounting hole
Clean the third hole. | to drill out.

Step 3: Cleaning plastic parts (Cont).

Parts Needed:

- Greg’s Wade extruder

Tools Needed:

- Round file

Note the strings left around the hub hole after we used the drill bit. Those need to be cleaned with a round file.

The hub hole already cleaned is shown on the top right corner of this picture. Now look at the hinge hole in the center of the picture. That one also needs cleaning.

Use the same round file to clean the idler hinge. Clean the hole as well as the outside. You can compare it to the uncleaned part on previous picture

Use the round file to clean any strings left on the hub hole

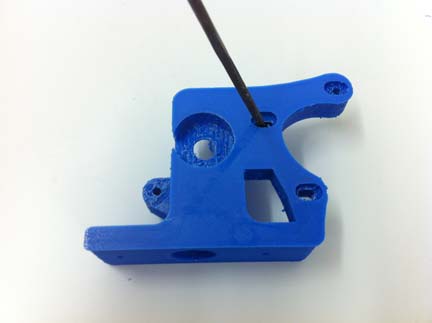
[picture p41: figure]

Clean the 3 motor mount holes using the round file. Don’t forget to also clean the recess holes where the screw head will go in .

Clean out the plastic extrusion hole using the same 1/8” drill bit.

Step 4: Cleaning plastic parts (Cont).

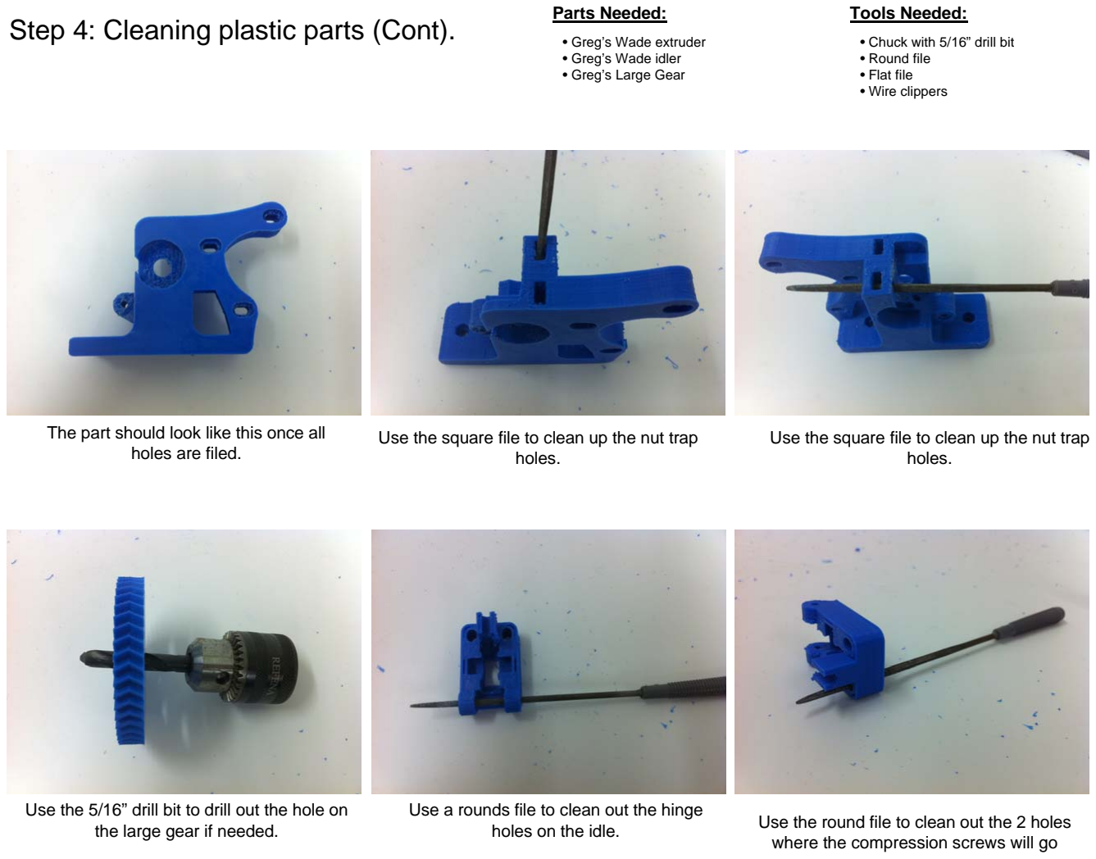
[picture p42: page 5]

Parts Needed:

- Greg’s Wade extruder
- Greg’s Wade idler
- Greg’s Large Gear

Tools Needed:

- Chuck with 5/16” drill bit
- Round file
- Flat file
- Wire clippers

Use the 5/16” drill bit to drill out the hole on the large gear if needed.

Use a rounds file to clean out the hinge
holes on the idle. | Use the round file to clean out the 2 holes where the compression screws will go

Use the square file to clean up the nut trap holes.

The part should look like this once all
holes are filed. | Use the square file to clean up the nut trap holes.

## Step 5: Wade-idler assembly

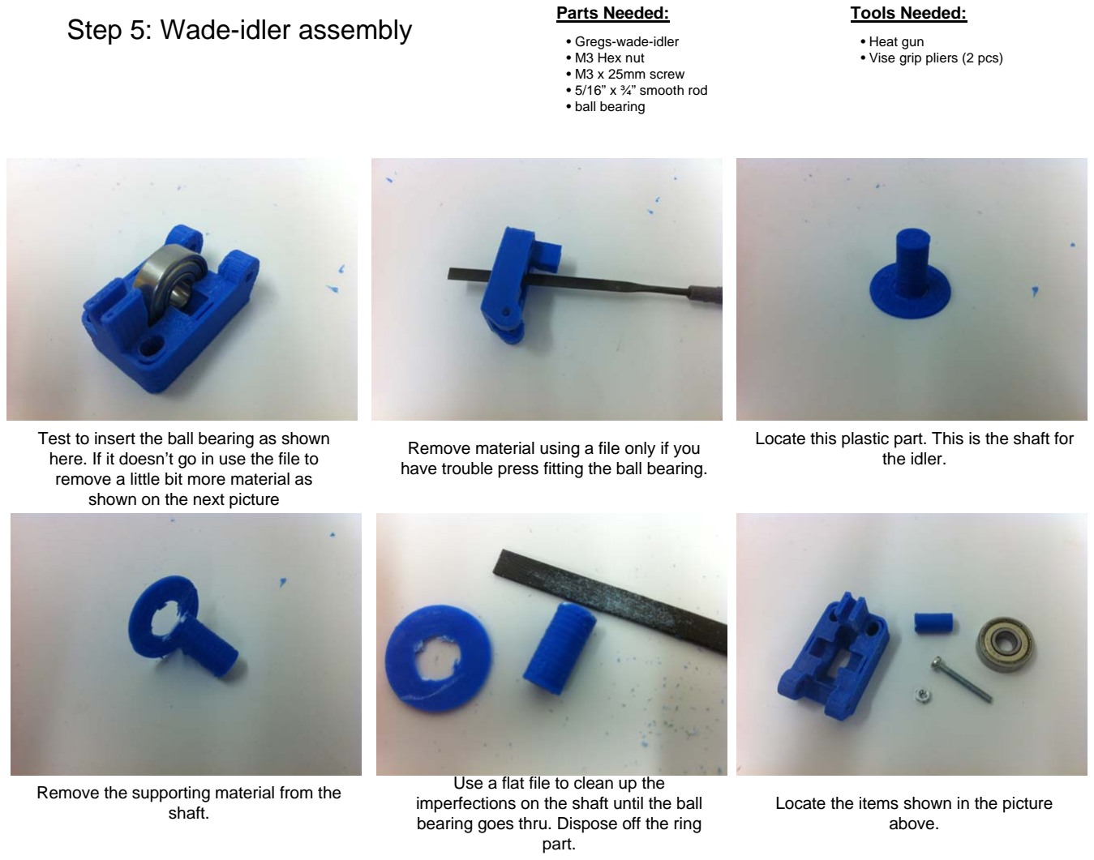
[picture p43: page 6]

Parts Needed:

- Gregs-wade-idler
- M3 Hex nut
- M3 x 25mm screw
- 5/16” x ¾” smooth rod
- ball bearing

Tools Needed:

- Heat gun
- Vise grip pliers (2 pcs)

Locate this plastic part. This is the shaft for the idler.

Use a flat file to clean up the imperfections on the shaft until the ball bearing goes thru. Dispose off the ring part.

Remove the supporting material from the
shaft. | Locate the items shown in the picture above.

Test to insert the ball bearing as shown here. If it doesn’t go in use the file to remove a little bit more material as shown on the next picture

Remove material using a file only if you have trouble press fitting the ball bearing.

## Step 6: Wade-idler assembly (cont.)

Parts Needed:

- Gregs-wade-idler
- M3 Hex nut
- M3 x 25mm screw
- 5/16” x ¾” smooth rod
- ball bearing

Tools Needed:

- Heat gun
- Vise grip pliers (2 pcs)

Place the shaft and ball bearing on top of the idler block

Now take the smooth rod and insert it into the ball bearing as shown.

This is how the idler assembly should look.

Insert the M3 x 25mm screw as shown and crew in the M3 nut. Then pull the screw to get the nut into the trap. If it doesn’t go in use the heat gun to soften the plastic around it.

Use the vise grip pliers to press fit into position.

This is how it should look after inserting the nut

## Step 7: Small gear assembly

Parts Needed:

- Small Gear
- 3mm setscrew
- M3 Hex nut

Tools Needed:

- Allen Key #1.5 (Metric)
- Wire clippers
- Chuck with 1/8” drill bit
- Chuck with 5mm” drill bit

Use the chuck with the 1/8” drill bit to clean out the hole for the setscrew as shown on the picture above.

Place the M3 nut on the nut trap and press in position using the nose pliers.

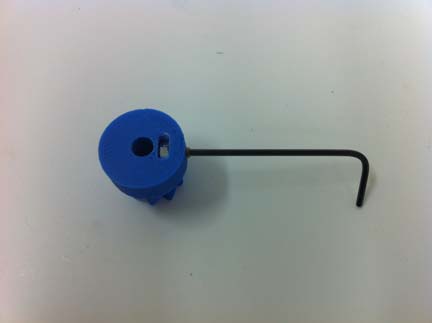
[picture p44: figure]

Use the Allen key #1.5 to screw-in the setscrew as shown on the picture above. Do not go past the shaft hole.

Use the square file to clean the nut trap.

This is how the nut should look. Also you can see the setscrew next to the gear.

Use chuck with a 5mm drill bit to drill out the hole where the shaft will be. Then use a round file to finish up the part until if fits tightly into the motor shaft.

## Step 8: extruder and large gear assembly

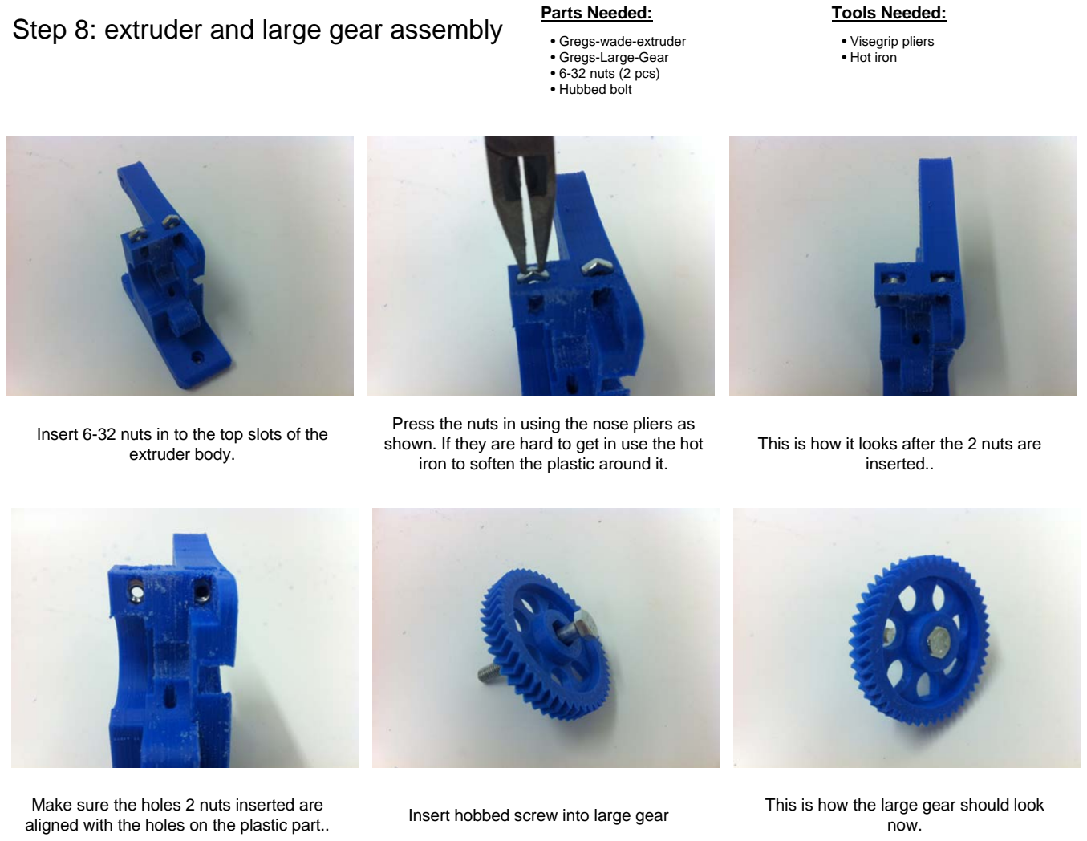
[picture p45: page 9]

Parts Needed:

- Gregs-wade-extruder
- Gregs-Large-Gear
- 6-32 nuts (2 pcs)
- Hubbed bolt

Tools Needed:

- Visegrip pliers
- Hot iron

This is how it looks after the 2 nuts are inserted..

Make sure the holes 2 nuts inserted are aligned with the holes on the plastic part..

This is how the large gear should look now.

Insert 6-32 nuts in to the top slots of the extruder body.

Insert hobbed screw into large gear

Press the nuts in using the nose pliers as shown. If they are hard to get in use the hot iron to soften the plastic around it.

## Step 9: extruder assembly (cont.)

Parts Needed:

- Gregs-Wade-extruder
- Gregs-Wade-idler
- Bearing plastic spacer
- M3 Hex nuts (2 pcs)
- Ball bearing (2 pcs)
- M3 x 25mm screw

Tools Needed:

- Heat gun
- philips screwdriver

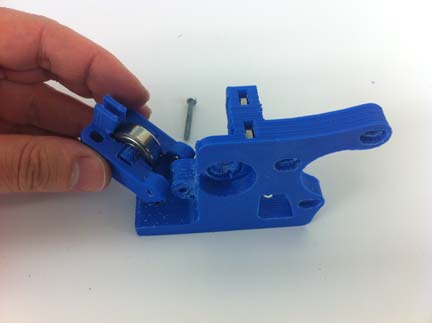
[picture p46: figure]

Insert the idler into the hinge of the extruder body. Start on the side where the trapped nut is. Be carefull not to pop out the nut.

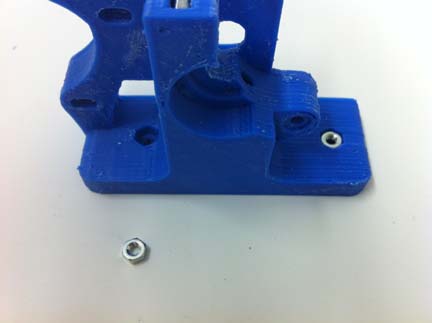
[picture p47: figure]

Once the idler is in position, proceed to screw-in the idler screw as shown in this and next pictures.

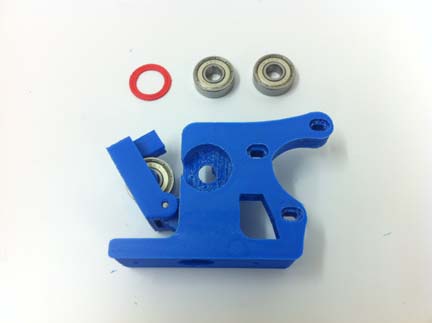
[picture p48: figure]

Locate two more of the ball bearings and the bearing spacer.

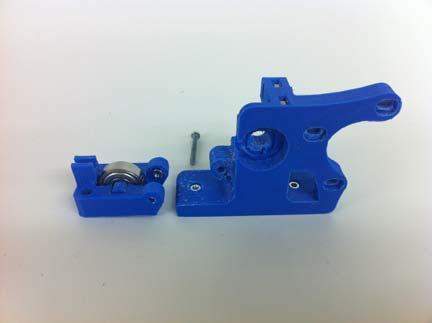
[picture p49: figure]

Position the idler and extruder parts as shown in the picture. We will assembly the idler into the extruder

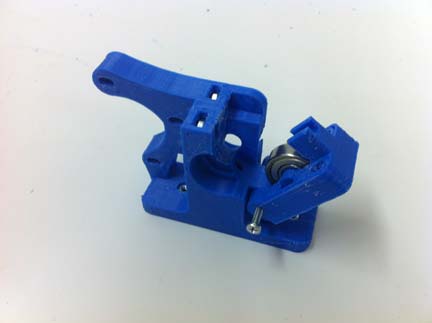
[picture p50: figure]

Make sure the screw is inserted in the proper direction. Should be inserted as shown here.

Take 2 of M3 hex nuts and the Gregs-wade-extruder. Insert the nuts on the base nut traps that are shown next to the nuts on the picture.

## Step 10: extruder assembly (cont.)

Parts Needed:
- Gregs-wade-extruder assembly
- Gregs-wade-idler assembly
- Bearing plastic spacer
- Large Gear assembly
- Ball bearings (2 pcs)
- 5/16 washers (9 pcs)
- M8 hex nut (2 pcs)

Tools Needed:

- Vise grip pliers

Press fit the ball bearing on top of the plastic bearing spacer.

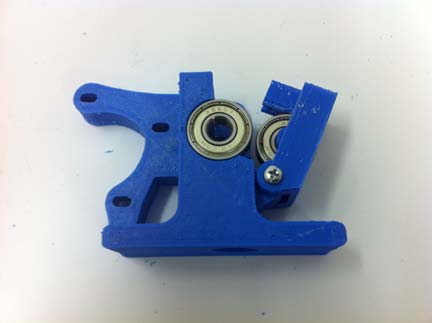
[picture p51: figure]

Flip the assembly over and press fit the second ball bearing

Tighten the first M8 nut then use the second M8 nut to jam in position. After tightening you might notice the bolt gets miss aligned. This is normal as tightening pushed the bearings to final position. Re-align changing washers and tighten again.

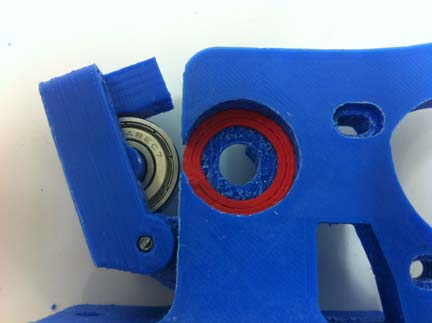
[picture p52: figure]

Press fit the plastic bearing spacer in position. Use the screw driver or file to push it ensure it goes all the way.

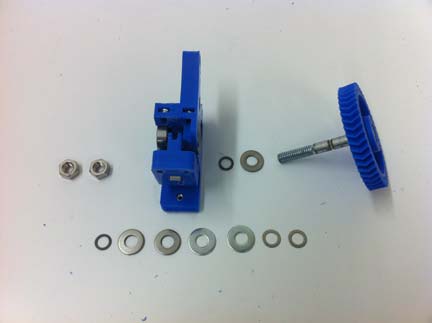
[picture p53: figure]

Locate the following parts. Note the additional washers and shoulders of various thicknesses. You will have to find the right combination to align the grubs on the bolt with the filament hole.

Insert the plastic bearing spacer as shown on the picture above

## Step 11: Extruder assembly (Cont.)

Parts Needed:

- Gregs-wade-extruder assembly
- 6-32 x 2” screws (2 pcs)
- 6-32 washers (4 pcs)
- springs
- Extruder motor
- small gear.
- M3 x 12 mm screws (3 pcs)

Tools Needed:

- Allen Key #1.5 (Metric))
- philips screwdriver

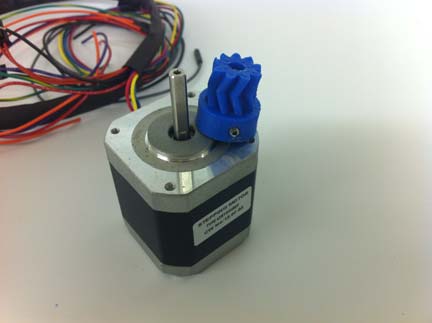
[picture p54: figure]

Align the setscrew with the flat on the motor shaft. Insert the gear on the motor shaft. Keep the alignment of the setscrew with the flat in the shaft


Use 3 screws to attach the motor as shown. Note the direction the wires are coming out of the motor. Do not tight completely yet.

Screw-in until it grabs the trapped nut on the extruder body. It should look like this.


Do not tight completely yet. Just enough so that it doesn’t rotate but still able to slide in and out

Locate the following items. Take the screw and insert the following: washer, spring, washer, idler, extruder.


Align the teeth on the gears by sliding in/out the small gear and slide the motor in all the way so that both gears are in full contact then tighten the motor screws.

## Step 12: Extruder assembly (Cont.)


Parts Needed:

- Plate
- Hotend
- Extruder Assembly

Tools Needed:

- Your Hands

Slide the hot end into the mounting plate. Make sure the wires are facing the open end of the plate.

Insert the hot end into the hole on the extruder. It should be a tight fit. If hard to get in try filing a little bit around the edge.

Locate the hot end tip and the mounting plate

This is how it should look. Note the orientation of the hotend wires as well as the motor wires.

Next, Tighten the setscrew on the small gear using the #1.5 Allen Key

Flip over the extruder assembly and position the hot end assembly as shown.

## Step 13: Mounting the Extruder assembly

Parts Needed:

- Gregs-wade-extruder assembly
- Frame Assembly
- M3 x 20 mm screws (3 pcs)

Tools Needed:

- philips screwdriver

Make sure the hotend goes into the hole. Notice there are 3 small holes on each side of the carriage. You want to use the middle ones on next step.

Insert a second M3 x 20mm screw from underneath on the other side.

Take the extruder assembly and position it on top of the carriage.

Align the extruder over the second screw and screw in onto the M3 nut on the extruder base.

Next, Flip the Frame assembly over and finish tightening the 2 screws using a screwdriver.

Insert an M3 x 20mm screw from below into the carriage hole, align the extuder and then screw in onto the M3 nut on the extruder base.

Step 14: Installing the Fans.


Parts Needed:

- Fan Holder (2 pcs)
- Fan (2 pcs)
- M3 Hex nuts (8 pcs)
- M3 x 12mm screws (4 pcs)

Tools Needed:

- philips screwdriver
- round file
- flat file

Place the fan on the place holder. Make sure the nuts on the fan are facing out.

Use the Flat file to clean up the internal faces of the pivoting joint.

Use the round file to clean up the fan holes.

Insert hex nuts into fan nut traps (4 pcs).

Use the round file to clean up the pivot holes.

Secure the fan in place using 2 M3x12mm screws as shown. Use the hoes opposite to the pivot point.

NOTE: Repeat all the steps below for the second fan assembly.

## Step 15: Installing the Fans (cont.)


Parts Needed:

- Fan Assembly (2 pcs)
- M3 Hex nuts (2 pcs)
- M3 x 25mm screws (2 pcs)
- M3 x 12mm screws (4 pcs)
- Wire nuts (2 pcs)
- Zip Ties (2 pcs)

Tools Needed:

- philips screwdriver
- Nose pliers

Connect the hotend wires. Green/Green to Red/Red and Translucent/translucent to black/black.

Inser the fan assembly as shown and slide in an M3 x 25mm into the pivot joint.

Secure the screw in place using an M3 Hex nut n the opposite side

Use wire nuts (2 pcs) to join together the Fan wires (red/red to Green and black/black to Purple.

Pivot the Fan assembly to the horizontal position and insert M3 x 12mm screws on the 2 remaining fan holes and tighten.

Route the wire harness thru the hole next to the power supply and secure with 2 zip ties as shown.

NOTE: Repeat the first 3 steps below for the second fan assembly.

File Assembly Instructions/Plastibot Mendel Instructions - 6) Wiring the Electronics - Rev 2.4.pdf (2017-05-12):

# Mendel 3D Printer Assembly


# Section 6

# Wiring the Electronics

## Step 1: Y Endstop Assembly

Parts Needed:

- Micro switch with Brown wires
- M3 x 12mm screw (2 pcs)
- M3 Hex nut
- Plastic endstop holder (2 pcs)
- Frame Assembly

Tools Needed:

- Visegrip Pliers
- Philips screwdriver


Locate the endstop holders, M3 x 16mm screws and M2 hex nuts shown on the picture above.


Screw-in M3 x 12mm screws into the microswitch holes (2 holes) to make threads on them then remove the screws.


Insert an M3 nut in the nut trap as shown. Use the screw to help you press the nut in or worst case use visegrip pliers to press them in. Do it for both endstop holders.


Snap the endstop assembly into the smooth rod next to the Y motor as shown on the picture above and use an M3 x 16mm screw to tighten it to the rod.

Position your frame assembly so that the bottom panel is facing you and the Y-Motor is facing down. Locate the endstop switch that is next to the motor.


Using two M3 x 12mm screws, attach the microswitch to the endstop holder as shown above.

## Step 2: X Endstop Assembly


Parts Needed:

- Micro switch with Brown wires
- M3 x 12mm screw (2 pcs)
- M3 Hex nut
- Plastic endstop holder (2 pcs)
- Frame Assembly

Tools Needed:

- Visegrip Pliers
- Philips screwdriver

Locate the microswitch shown.

Screw-in M3 x 12mm screws into the microswitch holes (2 holes) to make threads on them then remove the screws.

Snap the endstop assembly onto the smooth rod next to the X idler as shown on the picture above

Using two M3 x 12mm screws, attach the microswitch to the endstop holder as shown above.

Use an M3 x 16mm screw to clamp it to the rod. Do not tight yet. Flip the endstop back up as in previous picture

Flip over your machine so that the back panel is facing you.

## Step 3: Z Endstop Assembly


Parts Needed:

- Micro switch with Brown wires
- M3 x 12mm screw (2 pcs)
- M3 Hex nut
- Plastic endstop holder (2 pcs)
- Frame Assembly

Tools Needed:

- Visegrip Pliers
- Philips screwdriver

Locate the micro switch shown as well as the plywood side spacer.

Screw-in M3 x 12mm screws into the microswitch holes (2 holes) to make threads on them then remove the screws.

Insert into the slots | Insert the second spacer.

Locate on the left panel the 2 slots shown on the picture above. They are directly below the X-end-motor almost at the bottom panel.

Insert the M3 x 20mm screws into one of the spacers

## Step 4: Fan Assembly


Parts Needed:

- Frame Assembly
- Fan
- Laser cut Fan Tray
- M3 x 25mm screws (4 pcs)
- M3 nuts (4 pcs)

Tools Needed:

- Philips screwdriver
Install the Fan Locate the Fan cutout shown above. It’s on the lower side of the right panel. | Locate the Fan Tray shown above. It will be installed on top of the fan.
Screw in the micro switch | This is how it should look once finished. Insert the endstop wire on the same hole where the X-Motor is

Step 5: Card Tray Assembly.

Parts Needed:

- Laser Cut Card tray
- Controller Card
- M3 x 25mm screw (3 pcs)
- M3 Hex nut (3 pcs)
- Heatsinks (4 pcs)
- Thermal Adhesive ( 4 pcs)

Tools Needed:

•Philips screwdriver


Install the controller card onto the Card Tray using 3 M3 x 25mm screws and M3 nuts. The screws insert from below and the nuts go on the top.


Locate the parts shown above. | This is how the Card Tray should look.

Install remaining two screws and nuts as shown.

Attach the Fan Tray. Ignore the fact that the wires are not on the slot… this is the only picture available to show the Fan Tray installed. The wires should be under the Fan and thru that slot.

Before Attaching, make sure you run the cables coming from the X motor, Z1 Motor and Z-end-stop below the fan and thru the slot on the Fan tray shown above.

Step 6: Card wiring.

Boxes in Red represent power coming

Yellow Black; POWER IN; Purple Green; POWER OUT BED; Orange Orange; POWER OUT EXTR. 0; MOTOR X; MOTOR Y; MOTOR Z1; MOTOR Z2; Yellow; Blue; Green; Red; MOTOR E0; MOTOR E1; POWER OUT; FANS; None Y; None Z; None; END STOPS (pairs); Black; Gray; THERMISTORS E0 BED E1; from the power supply. Boxes in Blue represent connections to motors and Heaters. Boxes in Green are for future expansion of dual extrusion.; reference on where to connect the wires. Steps for connection are on the next slide.; SOCKET FOR DRIVER FOR FUTURE SECOND EXTRUDER; PORT FOR COMPUTER- LESS LCD CONTROLLER

Do not start wiring yet. Just use this as

Step 7: Wire Bundling.

Parts Needed:

- Laser Cut Card tray
- Controller Card
- M3 x 25mm screw (3 pcs)
- M3 Hex nut (3 pcs)
- Heatsinks (4 pcs)
- Thermal Adhesive ( 4 pcs)

Tools Needed:

•Philips screwdriver


Continue connecting the power for the heated bed and Extruder 0, Extruder 0 Motor and endstop wires. Bundle cables and zip tie to the card tray as shown.


Using the diagram on the previous slide connect the X, Y, Z1, and Z2 motor wires, as well as Extruder 0 and Bed Thermistors. Bundle wires and zip tie to the card tray as shown


Bundle any wires left from the power supply around the Z1 motor. Alternatively you could trim them down but keeping them allows for quick addition of options later on.


Use a yellow and black wire from the power supply to connect to the led strip.

Bundle both Bundles of wires and zip tie and loop around. Attach the wire bundle losely to the card tray as shown. Do not tighten the zip tie. The wire bundle needs to be able to slide freely.


Use wire nuts to connect the brown wire on the Power Supply with one of the Orange Wires. Do the same with the green wire and one of the black ones.

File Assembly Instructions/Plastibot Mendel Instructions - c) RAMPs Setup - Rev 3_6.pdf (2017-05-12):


# Mendel 3D Printer Assembly


# Appendix Z

# RAMPs setup

Revision 3.6

## Step 1: Adding jumpers


Parts Needed: | Tools Needed:

Insert jumpers (3 on each pololu for a total of 15). Insert them with the metal part of the jumper facing up.

Push the mosfet transistor forward a little bit as shown.

Place the heatsink on the back of the mosfet with the screw hole on the top half and align the heatsink hole with the Mosfet hole.

Apply a small dib of thermal paste on the mosfet transistor. Use a small screwdriver to help spread it evenly.

Place the M3 x 6mm screw on a screwdriver and insert thru the front of the mosfet

Open the ESD bag and remove the RAMPs card. Locate the small bag with the jumpers and remove them.

- Plastibot Mendel Printer
- Computer
- Your hands

## Step 2: Adding Mosfet Heatsink


Parts Needed: | Tools Needed:

Grab the M3 nut with the nose pliers and
place it against the screw tip | Tighten the screw .

Remove one of the pololus from the ESD bag.

Plug the power connectors. | Grab it from the 2 edges without pins.

Wipe the excess thermal paste from the screw tip

- Plastibot Mendel Printer
- Computer
- Your hands

## Step 3: Adding Pololus


Parts Needed: | Tools Needed:

Use the ESD cushion to push down the pololu into position. Repeat for the remaining 4 pololus

Cut a piece of Kapton tape long enough to cover the row of 2 pololus and apply using the ceramic screwdriver to help stick the kapton tape.

Use the ceramic screw driver to fold and stick the kapton tape

Apply kapton tape on the other edge of the
pololus as shown | Repeat for the row of 3 pololus.

Place it on the base connector and align both rows of pins.

- Plastibot Mendel Printer
- Computer
- Your hands

## Step 4: Adding Heatsinks to Pololus


Parts Needed: | Tools Needed:

Place the heatsink on top of the integrated
circuit, but centered across the pin rows. Repeat for the remaining 4 pololus

Take a look at the pins underneath the RAMPs card and make sure all pins are parallel. If you see pins bended use te nose pliers to straighten them

Remove the arduino from the ESD bag
and place it on top of the antistatic sponge. | Place the RAMPs next to the arduino
| card as shown.

Take on of the heatsinks that came with the pololus. Remove the paper protector from the sticker.

- Plastibot Mendel Printer
- Computer
- Your hands

## Step 5: Pluging RAMPS to Arduino board


Parts Needed: | Tools Needed:

Turn 90 degrees on Z axis and align the double row of pins in the back.

Turn 90 degress on Z axis and align the third side.

Using your 2 thumbs and 2 index fingers press down the RAMPs until all pins are fully connected.

Place the RAMPs on top of the Arduino and align the first row of pins

- Plastibot Mendel Printer
- Computer
- Your hands

This is how it should look once properly connected. Golden pins fully covered by connector.

Set your multimeter to Measure DC voltage in the miliVolts range.

## Step 6: Limiting current to pololus

Parts Needed: | Tools Needed:


Insert the Ground lead (black lead) into the power connector negative setscrew as shown.


Plug the USB connector to the ramps and to the computer.


Use the ceramic screwdriver to adjust the variable resistor until multimeter reads 0.48 Volts.


Touch the variable resistor for E1 with the red test lead.

Repeat the same process for pololus X, Y, and E0.

Repeat the same process for pololu Z but adjust this ones to 0.72 Volts instead. .

- Plastibot Mendel Printer
- Computer
- Your hands

## Step 7: Loading the Firmware

Parts Needed: | Tools Needed:

Go to the plastibot folder you created earlier and create a subfolder called Firmware. Click the file you downloaded and extract to the firmware folder.

Open Arduino and from the menu select File/Open, Go to your plastibot folder and select the following file: plastibot/firmware/marlin/marlin.pde

Scroll down to line # 201. It should read like this: #define
DEFAULT_AXIS_STEPS_PER_UNIT {44.4444, 44.4444, 2560, 767}


That should open a bunch of files. Look for the tab called “Configuration.h” and click on it.


The last value of 767 is the default number of steps per 1mm of extrusion. Write down that number. You will need it later on.

Go to www.plastibot.com/downloads and download the latest firmware corresponding to your setup (ie. Standard, heated bed, etc)

- Plastibot Mendel Printer
- Computer
- Your hands

## Step 8: Hotend Identification


Makergear Hotend has a black fiberglass insulator sleeve covering the nozzle

The Resistor J-Head Hotend has a bare square brass nozzle with resistor leads coming out on both sides

On your firmware, scroll down to line 92

The Heat Cartridge J-Head Hotend has all leads coming out of the same side of the aluminum nozzle and covered with kapton tape (kapton tape removed on picture above).

Enter a 1 if you have a MakerGear hotend. Enter a 5 if you have a Resistor J-Head Enter an 8 if you have a Heat Cartridge J-Head

Parts Needed: | Tools Needed:
- Plastibot Mendel Printer • Computer | • Your hands

Each hotend use a different Thermistor therefore need different tables on the firmware in order to provide accurate temperature readings.

## Step 9: Hotend Profile


On your firmware, scroll down to line 147 | Enable the corresponding profile for your hotend by removing the “//” for all 3 lines. Ensure the other profiles have “//” characters.
Parts Needed: | Tools Needed:
- Plastibot Mendel Printer • Computer | • Your hands


Each hotend uses a different heating element therefore needs different PID Profiles in the firmware in order to keep temperature in check.

## Step 10: Loading the Firmware (cont.)


Parts Needed: | Tools Needed:

On the arduino menu, select “Tools Serial Port COMxx, where xx is the port # that was assigned to your printer, usually a number higher than 4.

From the Arduino menu select File Upload to I/O board. Alternatively you could use the icon to upload.

Then after a couple of minutes if will change to “Done Uploading”

The bottom section will show “Uploading to I/O board”

That’s it. Save and Close the arduino program. Note that there may be more than one session open. Close all of them.

From the Arduino menu, select “Tools Board Arduino Mega 2560

- Plastibot Mendel Printer
- Computer
- Your hands

Step 11: Card wiring.

Red
Black
Red
Black

POWER IN

Purple
Green

POWER OUT
BED

Orange
Orange

POWER OUT
EXTR. 0

MOTOR
X

MOTOR
Y

MOTOR
Z1

MOTOR

MOTOR
E0

MOTOR
E1

POWER OUT
FANS

Purple
Green

END STOPS

(pairs) | Black Red Black Red Black Red

THERMISTORS
E0 BED E1

CAUTION: Remove any power source to the card inclusing USB connector before pluging any of the wires. Failure to remove power sources my cause damage to the pololus.
Connect the set of motors, endstops and extruders
as shown on the diagram. Connect the Power
supply Jack | Black Blue Green Red Black Blue Green Red | Black Blue Green Red | Black Blue Green Red | Black Blue Green Red

## Step 12: Installing Pronterface

Parts Needed: | Tools Needed:


Click “connect”. The status section will show you are connected. Proceed to plug the power cable on your printer to the electrical outlet and turn on the switch.


Make sure Port shows COMxx where xx is the port assigned to your printer. Make sure the communication speed is 250,000. Change Espeed to 100 and Zspeed to 100


Plug the USB cable to the RAMPS then Click the pronterface shortcut you just created. The following screen should open up.

Go to www.plastibot.com/downloads and download pronterface corresponding to your OS (i.e Windows or Mac)

Click on the file you downloaded and extract into the Plastibot folder.

That should create a folder called Pronterface. Navigate to that folder and right click the file “pronterface.exe”. Then from the menu select to create a shortcut and move the shortcut to your desktop.

- Plastibot Mendel Printer
- Computer
- Your hands

## Step 13: Validating Motors and Endstops function

Parts Needed: | Tools Needed:

On Pronterface click on the right +X arrow for the ring that shows a value of 1. that should move the X Carriage by 1mm to the right.

You should see the shaft of Motor X turn clockwise slightly (about 1/20th of a turn) and get fully energized meaning you won’t be able to move the shaft.

Repeat the previous steps for the Y and Z carriages. Document your findings

Repeat for –X. clicking the ring with -10. It should move counterclockwise about ½ turn. Now keep pressed the X endstop switch with your finger, and click on -10 once again. At this time there should be no movement. If there is movement take note and we will troubleshoot on the next step.

If movement direction is NOT correct then take note of that. We will fix on the next step. If there is no movement at all also take note and we will fix on the next step.

Now click on the ring showing 10, and verify that it actually moves about ½ turn.

- Plastibot Mendel Printer
- Computer
- Pronterface
- Your hands
- Ruler

## Step 14: Validating Heaters and Extruder

motor; Parts Needed:; Tools Needed:; Once the heater reached temperature,; other way take note.; until the Heater thermometer shows 215. Make sure “Monitor Printer” is selected otherwise thermometer won’t update.; Click the heater off.; temperature.; • Plastibot Mendel Printer • Computer; • Your hands; temperature won’t update on Thermometer.; Grab the hotend nozzle with the helping get hot.; Click the Bed off.

click on the extrude button. The Extruder Motor should turn clockwise. If it turns the

On Pronterface, set the heater temperature to 215 and click set then wait a couple minutes

Set the Bed Temperature to 100 and click set. Check the Thermometer to see if it’s raising. It will take about 10 min to reach

NOTE: Make sure “Monitor Printer” is selected otherwise

hands so that it hangs on the air as it will

Step 15: Troubleshooting Motors, Endstops and Heaters.
The following matrix shows common problems, it’s root cause and possible solutions. Use it to solve any problems found on the 2 previous steps. Make sure the printer is turned off and unplugged before doing any change.

Hotend or
Bed Heating
Element

X, Y, Z, E
Motors
Category | Problem | Possible Root Cause | Possible Solution
| Motor spins in the opposite direction | Connector is connected backwards | Disconnect, turn the connector 180 degrees and reconnect.
| Motor doesn’t move at all | Cable disconnected or connected in the wrong place? | Connect properly
| Motor is connected but it doesn’t move at all | One of the wires in the connector could not be making contact | Verify all 4 cables on the connector to ensure the crimps are all the way into the plastic receptacle. Use a multimeter (if available) to check continuity on the motor wire. Each set of adjacent wires on the connector should read between 1.4 and 4 Ohms.
| Motor makes like it tries to move but it doesn’t | One of the wires in the connector could not be making contact | Verify all 4 cables on the connector to ensure the crimps are all the way into the plastic receptacle. Use a multimeter (if available) to check continuity on the motor wire. Each set of adjacent wires on the connector should read a couple Ohms.
| Heater is not heating up. | Cable disconnected or connected in the wrong place? | Connect properly
| Heater is properly connected but still not heating up | One of the cables on the connector might not be making contact | Use a multimeter (if available) to check continuity on the heater wires (red to red wires on the Hotend, Green to purple wires on Heated Bed). It should read around 6 Ohms for hotend and ~2 Ohms for Heated Bed.
| Heater is properly connected, measures continuity, yet is not heating up. | Thermistor properly connected? | Connect properly
| Heater is properly connected, measures continuity, Thermistor is connected, yet is not heating up. | Thermistor connector not making contact. | Use a multimeter (if available) to check continuity on the Thermistor wires (grey/grey wires) It should read around 100 KOhms.

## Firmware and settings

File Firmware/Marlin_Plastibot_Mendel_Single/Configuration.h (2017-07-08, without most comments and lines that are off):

#define CONFIGURATION_H
#define STRING_VERSION_CONFIG_H __DATE__ " " __TIME__ // build date and time
#define STRING_CONFIG_H_AUTHOR "(Freeman @ Plastibot)" // Who made the changes.
#define SERIAL_PORT 0
#define BAUDRATE 250000
#define MOTHERBOARD 33
#define CUSTOM_PRINTER_NAME "Plastibot"
#define EXTRUDERS 1
#define POWER_SUPPLY 1
#define TEMP_SENSOR_0 8
#define TEMP_SENSOR_1 0
#define TEMP_SENSOR_2 0
#define TEMP_SENSOR_BED 1
#define MAX_REDUNDANT_TEMP_SENSOR_DIFF 10
#define TEMP_RESIDENCY_TIME 5  // (seconds)
#define TEMP_HYSTERESIS 3       // (degC) range of +/- temperatures considered "close" to the target one
#define TEMP_WINDOW     1       // (degC) Window around target to start the residency timer x degC early.
#define HEATER_0_MINTEMP 5
#define HEATER_1_MINTEMP 5
#define HEATER_2_MINTEMP 5
#define BED_MINTEMP 5
#define HEATER_0_MAXTEMP 300
#define HEATER_1_MAXTEMP 300
#define HEATER_2_MAXTEMP 300
#define BED_MAXTEMP 150
#define PIDTEMP
#define BANG_MAX 255 // limits current to nozzle while in bang-bang mode; 255=full current
#define PID_MAX 255 // limits current to nozzle while PID is active (see PID_FUNCTIONAL_RANGE below); 255=full current
  #define PID_FUNCTIONAL_RANGE 10 // If the temperature difference between the target temperature and the actual temperature
  #define PID_INTEGRAL_DRIVE_MAX 255  //limit for the integral term
  #define K1 0.96 //smoothing factor within the PID
  #define PID_dT ((OVERSAMPLENR * 8.0)/(F_CPU / 64.0 / 256.0)) //sampling period of the temperature routine
    #define  DEFAULT_Kp 34.85
    #define  DEFAULT_Ki 2.87
    #define  DEFAULT_Kd 105.64
#define PIDTEMPBED
#define MAX_BED_POWER 255 // limits duty cycle to bed; 255=full current
  #define  DEFAULT_bedKp 162.50
  #define  DEFAULT_bedKi 9.88
  #define  DEFAULT_bedKd 668.28
#define PREVENT_DANGEROUS_EXTRUDE
#define PREVENT_LENGTHY_EXTRUDE
#define EXTRUDE_MINTEMP 120
#define EXTRUDE_MAXLENGTH (X_MAX_LENGTH+Y_MAX_LENGTH) //prevent extrusion of very large distances.
#define ENDSTOPPULLUPS // Comment this out (using // at the start of the line) to disable the endstop pullup resistors
  #define ENDSTOPPULLUP_XMAX
  #define ENDSTOPPULLUP_YMAX
  #define ENDSTOPPULLUP_ZMAX
  #define ENDSTOPPULLUP_XMIN
  #define ENDSTOPPULLUP_YMIN
  #define ENDSTOPPULLUP_ZMIN
const bool X_MIN_ENDSTOP_INVERTING = true; // set to true to invert the logic of the endstop.
const bool Y_MIN_ENDSTOP_INVERTING = true; // set to true to invert the logic of the endstop.
const bool Z_MIN_ENDSTOP_INVERTING = true; // set to true to invert the logic of the endstop.
const bool X_MAX_ENDSTOP_INVERTING = true; // set to true to invert the logic of the endstop.
const bool Y_MAX_ENDSTOP_INVERTING = true; // set to true to invert the logic of the endstop.
const bool Z_MAX_ENDSTOP_INVERTING = true; // set to true to invert the logic of the endstop.
#define DISABLE_MAX_ENDSTOPS
#if defined(COREXY) && !defined(DISABLE_MAX_ENDSTOPS)
  #define DISABLE_MAX_ENDSTOPS
#endif
#define X_ENABLE_ON 0
#define Y_ENABLE_ON 0
#define Z_ENABLE_ON 0
#define E_ENABLE_ON 0 // For all extruders
#define DISABLE_X false
#define DISABLE_Y false
#define DISABLE_Z true
#define DISABLE_E false // For all extruders
#define INVERT_X_DIR false    // for Mendel set to false, for Orca set to true
#define INVERT_Y_DIR false    // for Mendel set to true, for Orca set to false
#define INVERT_Z_DIR false     // for Mendel set to false, for Orca set to true
#define INVERT_E0_DIR false   // for direct drive extruder v9 set to true, for geared extruder set to false
#define INVERT_E1_DIR false    // for direct drive extruder v9 set to true, for geared extruder set to false
#define INVERT_E2_DIR false   // for direct drive extruder v9 set to true, for geared extruder set to false
#define X_HOME_DIR -1
#define Y_HOME_DIR -1
#define Z_HOME_DIR -1
#define min_software_endstops false // If true, axis won't move to coordinates less than HOME_POS.
#define max_software_endstops true  // If true, axis won't move to coordinates greater than the defined lengths below.
#define X_MAX_POS 200
#define X_MIN_POS 0
#define Y_MAX_POS 228
#define Y_MIN_POS 0
#define Z_MAX_POS 200
#define Z_MIN_POS 0
#define X_MAX_LENGTH (X_MAX_POS - X_MIN_POS)
#define Y_MAX_LENGTH (Y_MAX_POS - Y_MIN_POS)
#define Z_MAX_LENGTH (Z_MAX_POS - Z_MIN_POS)
#define MANUAL_X_HOME_POS 0
#define MANUAL_Y_HOME_POS 0
#define MANUAL_Z_HOME_POS 0
#define NUM_AXIS 4 // The axis order in all axis related arrays is X, Y, Z, E
#define HOMING_FEEDRATE {50*60, 50*60, 8*60, 0}  // set the homing speeds (mm/min)
#define DEFAULT_AXIS_STEPS_PER_UNIT   {44.4444,80.0,2560,856}  // default steps per unit for Plastibot Mendel {X,Y,Z,E}
#define DEFAULT_E1_STEPS_PER_UNIT     800                    // default steps per unit for second extruder
#define DEFAULT_MAX_FEEDRATE          {500, 500, 2, 45}      // (mm/sec)
#define DEFAULT_MAX_ACCELERATION      {9000,9000,100,100}  // X, Y, Z, E maximum start speed for accelerated moves. E default values are good for skeinforge 40+, for older versions raise them a lot.
#define DEFAULT_ACCELERATION          500    // X, Y, Z and E max acceleration in mm/s^2 for printing moves
#define DEFAULT_RETRACT_ACCELERATION  3000   // X, Y, Z and E max acceleration in mm/s^2 for retracts
#define EXTRUDER_OFFSET_X {0.0, 0.00} // (in mm) for each extruder, offset of the hotend on the X axis
#define EXTRUDER_OFFSET_Y {0.0, 66.20}  // (in mm) for each extruder, offset of the hotend on the Y axis
#define DEFAULT_XYJERK                8.0    // (mm/sec)
#define DEFAULT_ZJERK                 0.4     // (mm/sec)
#define DEFAULT_EJERK                 10.0    // (mm/sec)
#define EEPROM_SETTINGS
#define EEPROM_CHITCHAT
#define TPU_PREHEAT_HOTEND_TEMP 230
#define TPU_PREHEAT_HPB_TEMP 50
#define TPU_PREHEAT_FAN_SPEED 0   // Insert Value between 0 and 255
#define PLA_PREHEAT_HOTEND_TEMP 185
#define PLA_PREHEAT_HPB_TEMP 60
#define PLA_PREHEAT_FAN_SPEED 0   // Insert Value between 0 and 255
#define HIPS_PREHEAT_HOTEND_TEMP 230
#define HIPS_PREHEAT_HPB_TEMP 110
#define HIPS_PREHEAT_FAN_SPEED 0   // Insert Value between 0 and 255
#define ABS_PREHEAT_HOTEND_TEMP 230
#define ABS_PREHEAT_HPB_TEMP 110
#define ABS_PREHEAT_FAN_SPEED 0   // Insert Value between 0 and 255
#define REPRAP_DISCOUNT_FULL_GRAPHIC_SMART_CONTROLLER
 #define DOGLCD
 #define U8GLIB_ST7920
 #define REPRAP_DISCOUNT_SMART_CONTROLLER
 #define ULTIPANEL
 #define NEWPANEL
  #define SDSUPPORT
  #define ULTRA_LCD
    #define LCD_WIDTH 20
    #define LCD_HEIGHT 5
#  define DEFAULT_LCD_CONTRAST 32
#define FAST_PWM_FAN
#define SOFT_PWM_SCALE 0
#include "Configuration_adv.h"
#include "thermistortables.h"

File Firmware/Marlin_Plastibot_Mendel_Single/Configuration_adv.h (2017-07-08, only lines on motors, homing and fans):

#define CASEFAN_PIN -1 //Pin used for the fan to cool controller (-1 to disable)
#define X_HOME_RETRACT_MM 5
#define Y_HOME_RETRACT_MM 5
#define Z_HOME_RETRACT_MM 4
#define QUICK_HOME  //if this is defined, if both x and y are to be homed, a diagonal move will be performed initially.
#define MICROSTEP1 LOW,LOW
#define MICROSTEP2 HIGH,LOW
#define MICROSTEP4 LOW,HIGH
#define MICROSTEP8 HIGH,HIGH
#define MICROSTEP16 HIGH,HIGH
#define MICROSTEP_MODES {16,16,16,16,16} // [1,2,4,8,16]
#define DIGIPOT_MOTOR_CURRENT {175,175,240,135,135} // Values 0-255 (RAMBO 135 = ~0.75A, 185 = ~1A)

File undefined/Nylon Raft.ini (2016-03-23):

[profile]
layer_height = .2
wall_thickness = 1.2
retraction_enable = True
solid_layer_thickness = 1.2
fill_density = 25
nozzle_size = 0.4
print_speed = 30
print_temperature = 270
support = Touching buildplate
platform_adhesion = Raft
filament_diameter = 2.85
filament_flow = 100.0
retraction_speed = 60.0
retraction_amount = 1.5
retraction_min_travel = 1.5
retraction_combing = True
retraction_minimal_extrusion = 0.02
retraction_hop = 0.0
bottom_thickness = 0.0
layer0_width_factor = 100
travel_speed = 100
bottom_layer_speed = 30
infill_speed = 0
inset0_speed = 0.0
insetx_speed = 0.0
cool_min_layer_time = 20
fan_enabled = True
skirt_line_count = 0
skirt_gap = 3.0
skirt_minimal_length = 150.0
fan_full_height = 0
fan_speed = 100
fan_speed_max = 100
cool_min_feedrate = 5
cool_head_lift = False
solid_top = True
solid_bottom = True
fill_overlap = 10
support_type = Grid
support_angle = 60
support_fill_rate = 15
support_xy_distance = 0.7
support_z_distance = 0.15
spiralize = False
simple_mode = False
brim_line_count = 20
raft_margin = 5.0
raft_line_spacing = 3.0
raft_base_thickness = 0.3
raft_base_linewidth = 1.0
raft_interface_thickness = 0.27
raft_interface_linewidth = 0.4
raft_airgap_all = 0.0
raft_airgap = 0.1
raft_base_speed = 30
raft_surface_speed = 30
raft_surface_layers = 2
raft_surface_thickness = 0.27
raft_surface_linewidth = 0.4
fix_horrible_union_all_type_a = True
fix_horrible_union_all_type_b = False
fix_horrible_use_open_bits = False
fix_horrible_extensive_stitching = False
plugin_config =
object_center_x = -1
object_center_y = -1

[alterations]
start.gcode = ;Sliced at: {day} {date} {time}
        ;Basic settings: Layer height: {layer_height} Walls: {wall_thickness} Fill: {fill_density}
        ;Print time: {print_time}
        ;Filament used: {filament_amount}m {filament_weight}g
        ;Filament cost: {filament_cost}
        ;M190 S{print_bed_temperature} ;Uncomment to add your own bed temperature line
        ;M109 S{print_temperature} ;Uncomment to add your own temperature line
        G21        ;metric values
        G90        ;absolute positioning
        M82        ;set extruder to absolute mode
        M106       ;start with the fan on
        G28 X0 Y0  ;move X/Y to min endstops
        G28 Z0     ;move Z to min endstops
        G1 Z15.0 F{travel_speed} ;move the platform down 15mm
        G92 E0                  ;zero the extruded length
        G1 F100 E10             ;extrude 10mm of feed stock
        G92 E0                  ;zero the extruded length again
        G1 F{travel_speed}
        ;Put printing message on LCD screen
        M117 Printing...
end.gcode = ;End GCode
        M104 S0                     ;extruder heater off
        M140 S0                     ;heated bed heater off (if you have it)
        G91                                    ;relative positioning
        G1 E-1 F300                            ;retract the filament a bit before lifting the nozzle, to release some of the pressure
        G1 Z+0.5 E-5 X-20 Y-20 F{travel_speed} ;move Z up a bit and retract filament even more
        G28 X0 Y0                              ;move X/Y to min endstops, so the head is out of the way
        G1 Y190                                                                  ;move Y to front
        M84                         ;steppers off
        G90                         ;absolute positioning
        ;{profile_string}
support_start.gcode =
support_end.gcode =
cool_start.gcode =
cool_end.gcode =
replace.csv =
preswitchextruder.gcode = ;Switch between the current extruder and the next extruder, when printing with multiple extruders.
        ;This code is added before the T(n)
postswitchextruder.gcode = ;Switch between the current extruder and the next extruder, when printing with multiple extruders.
        ;This code is added after the T(n)

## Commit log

2013-06-04 Initial Release to the Public
    [Bracket.scad, Bracket.stl, Extruder-all-parts.scad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]
2015-03-10 add frog bracket and card bracket to plastic parts
    [Card Bracket 10.stl, Card Bracket 15.stl, Card Bracket.scad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]
2016-03-23 Octoprint for Raspberry Pi
    Intallation Instructions:
    Make sure you have a good connection to the internet on your Raspberry Pi.
    Make sure you have the Raspbian operating system. (This was made on version Wheezy).
    Login as root user by typing "su" followed by a password (don't type the quotes).
    Save the file "OctoprintInstall.sh" in the home directory of your Raspberry Pi (/home/pi)
    Type this in the command line:
    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
2016-04-12 Added files via upload
    A sample video, printing on a Plastibot printer using Octoprint to create a time-lapse movie.
    This print uses a cardboard build plate with no heated bed. This works fine for PLA.
2017-05-12 added folder with 1.75mm extruder
    [Extruder-all-parts-1_75.scad, Extruder-idler-primary-1_75.stl, Extruder-primary_body-1_75-fixed.stl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]
2017-05-12 added other diameters for spool bushings
    [Extruder-all-parts.scad, Extruder-all-parts.stl, bushing-1Kg-32mm.scad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]
2017-05-12 added bed corners for new heated bed design
    [Bed-Corner-std-nut-3_5mm.scad, Bed-Corner-std-nut-3_5mm.stl]
2017-05-12 Added backlash spring cup to eliminate backlash spring binding
    [Spring Cup Rev1.scad, Spring Cup Rev1.stl, Spring Cup.scad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]
2017-05-12 added assembly instructions folder
2017-05-21 added code for Hexagon Fan mount bracket and duct
    [Hexagon_Fan_Duct_Rev5.scad, Hexagon_Fan_Duct_Rev5.stl, hotend_fan_rev1.stl]
2017-07-08 Added Firmware folder
    [Configuration.h, Configuration_adv.h]
